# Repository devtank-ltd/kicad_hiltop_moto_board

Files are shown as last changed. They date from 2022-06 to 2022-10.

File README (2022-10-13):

Copyright Devtank Ltd 2021.

This documentation describes Open Hardware and is Licensed under CERN-OHL-W v2.

You may redistribute and modify this documentation under the terms of the CERN-OHL-W v2 (https://cern.ch/cern-ohl). This documentation is distributed WITHOUT ANY EXPRESS OR IMPLIED WARRANTY, INCLUDING OF MERCHANTABILITY, SATISFACTORY QUALITY AND FITNESS FOR A PARTICULAR PURPOSE. Please see the CERN-OHL-W v2 for applicable conditions

Source location: git@github.com:devtank-ltd/kicad_hiltop_loti_board.git 

As per CERN-OHL-W v2 section 4.1, should You produce hardware based on these sources, You must maintain the Source Location visible on the external case of the HILTOP or other product you make using this documentation.

This folder contains HILTOP Moto Board hardware schematics and pcb layout files 

You will need Kicad to open hardware design files.

Moto Boards and other test and measurement products can be purchased directly from Devtank Ltd.

Please contact:
Tim Telford
CTO - Devtank Ltd
+44 (0)1332 650944

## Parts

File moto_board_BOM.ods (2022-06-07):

Title | Moto Board
Revision | Draft
Date | 2019-10-01
Generated | Mon 18 Nov 2019 14:30:10 GMT
Company | Devtank LTD
Comment 1
Comment 2
Comment 3
Comment 4
Total Parts | 204
Total Unique Parts | 68
Ref | Qty | Value | Footprint | Devtank | Dielectric | ESR | Tolerance | Voltage | Voltage | Description | Manufacturer | Manufacturer Part Number | Supplier | Supplier Part number | Cost (unit) | Cost (total)
C1 | 1 | 1uF | Capacitor_SMD:C_0603_1608Metric | 105-014 | X7R |  |  | 16V |  | 1uF 16V X7R | Walsin | 0603B105K160CT | Farnell | 2496835 | 0.128 | 0.128
C2 | 1 | 0.1uF | Capacitor_SMD:C_0402_1005Metric | 105-019 | X7R |  |  | 16V |  | 100nF 50V X7R | Murata Electronics | GRM155R71H104ME14D | Digikey | 490-10701-1-ND | 0.032 | 0.032
C3 | 1 | 0.1uF | Capacitor_SMD:C_0402_1005Metric | 105-019 | X7R | LOW |  |  | 50V | 100nF 50V X7R | Murata Electronics | GRM155R71H104ME14D | Digikey | 490-10701-1-ND | 0.032 | 0.032
C4 | 1 | 0.01uF | Capacitor_SMD:C_0402_1005Metric | 105-029 |  | LOW |  | 50V |  | 0.01uF 50V X7R 0402 | Kemet | C0402C103K5RAC7411 | Mouser | 80-C0402C103K5R7411 | 0.017 | 0.017
C5 | 1 | 1uF | Capacitor_SMD:C_0603_1608Metric | 105-014 | X7R | LOW |  | 16V |  | 1uF 16V X7R | Walsin | 0603B105K160CT | Farnell | 2496835 | 0.128 | 0.128
C6 C7 | 2 | 0.1uF | Capacitor_SMD:C_0402_1005Metric | 105-019 |  |  |  | 50V |  | 100nF 50V X7R | Murata Electronics | GRM155R71H104ME14D | Digikey | 490-10701-1-ND | 0.032 | 0.064
C8 C9 C14 C15 C16 C17 C18 C19 | 8 | 100uF | Capacitor_SMD:CP_Elec_6.3x7.7 | 108-006 |  |  |  | 50V |  | 100uF 50V 0.34R MZR Series | United Chemi-Con | EMZR500ARA101MF80G | Mouser | 661-EMZR500ARA101MF8 | 0.429 | 3.432
C10 C11 | 2 | 10uF | Capacitor_SMD:C_0805_2012Metric | 105-001 |  |  |  |  |  | 10uF 16V X5R 10% MLCC | AVX | 0805YD106KAT2A | Farnell | 1658880 | 0.545 | 1.09
C12 C24 C56 C73 C74 C79 C80 | 7 | 100nF | Capacitor_SMD:C_0402_1005Metric | 105-019 |  |  |  |  |  | 100nF 50V X7R | Murata Electronics | GRM155R71H104ME14D | Digikey | 490-10701-1-ND | 0.032 | 0.224
C13 | 1 | 100uF | Capacitor_SMD:CP_Elec_6.3x7.7 | 108-006 |  |  |  |  |  | 100uF 50V 0.34R MZR Series | United Chemi-Con | EMZR500ARA101MF80G | Mouser | 661-EMZR500ARA101MF8 | 0.429 | 0.429
C52 | 1 | DNF | Capacitor_SMD:C_0603_1608Metric
C55 C102 C104 | 3 | 4.7uF | Capacitor_SMD:C_0402_1005Metric | 105-025 | X5R |  |  | 6.3V |  | 4.7uF 6.3V X5R | muRata | GRM155R60J475ME47D | Farnell | 2426952RL | 0.0565 | 0.1695
C75 C76 | 2 | 18pF | Capacitor_SMD:C_0603_1608Metric | 106-003 |  |  |  |  |  | 18pF COG/NPO | AVX | 06035A180JAT2A | Farnell | 1612182 | 0.0681 | 0.1362
C77 C78 | 2 | 4.3pF | Capacitor_SMD:C_0603_1608Metric | 106-014 |  |  |  |  |  | 4.3pF COG/NPO | Kemet | C0603C439D1HACTU | Mouser | 80-C0603C439D1HACTU | 0.019 | 0.038
C81 C82 | 2 | 100nF | Capacitor_SMD:C_0603_1608Metric | 105-002 |  |  |  |  |  | 100nF 50V X7R | Kemet | C0603C104M5RACTU | Farnell | 2581046 | 0.0413 | 0.0826
C88 C89 | 2 | 33pF | Capacitor_SMD:C_0603_1608Metric | 106-015 |  |  |  |  |  | 33pF COG/NPO | Multicomp Pro | MC0603N330J500CT | Farnell | 1759059 | 0.0311 | 0.0622
C90 | 1 | 0.1uF | Capacitor_SMD:C_0603_1608Metric | 105-002 |  |  |  |  |  | 100nF 50V X7R | Kemet | C0603C104M5RACTU | Farnell | 2581046 | 0.0413 | 0.0413
C91 | 1 | 1.0uF | Capacitor_SMD:C_0402_1005Metric | 105-026 | X5R |  |  | 16V |  | 1uf 16V X5R | Taiyo Yuden | EMK105BJ105KV-F | Farnell | 2113064 | 0.0415 | 0.0415
C92 C94 C95 C96 C97 C98 C99 C101 | 8 | 0.1uF | Capacitor_SMD:C_0402_1005Metric | 105-019 |  |  |  |  |  | 100nF 50V X7R | Murata Electronics | GRM155R71H104ME14D | Digikey | 490-10701-1-ND | 0.032 | 0.256
C100 C103 C105 | 3 | 4.7uF | Capacitor_SMD:C_0402_1005Metric | 105-025 | X5R |  |  | 6.3V |  | 4.7uF 6.3V X5R | muRata | GRM155R60J475ME47D | Farnell | 2426952RL | 0.0565 | 0.1695
C106 | 1 | DNF | Capacitor_SMD:C_0402_1005Metric
D1 | 1 | B240A-13 | Diode_SMD:D_SMA | 133-008 |  |  |  |  |  | B240A-13-F - Schottky Rectifier, 40 V, 2 A, Single, DO-214AC, 2 Pins, 500 mV | Diodes Inc. | B240A-13-F | Farnell | 1843669 | 0.308 | 0.308
D2 | 1 | RED | LED_SMD:LED_0603_1608Metric | 110-001 |  |  |  |  |  | Red LED | ROHM | SML-D12V8WT86C | Farnell | 2687488 | 0.218 | 0.218
D3 D4 D5 | 3 | GRN | LED_SMD:LED_0603_1608Metric | 110-002 |  |  |  |  |  | Green LED | Rohm Semiconductor | SML-D12P8WT86C | Farnell | 2687486 | 0.206 | 0.618
D13 | 1 | GRN | LED_SMD:LED_0603_1608Metric | 110-002 |  |  |  |  |  | Green LED | Rohm Semiconductor | SML-D12P8WT86C | Farnell | 2687486 | 0.214 | 0.214
D32 | 1 | MBR230LSFT1G | Diode_SMD:D_SOD-123 | 133-006 |  |  |  |  |  | Schottky Rectifier, 30 V, 2 A, Single, SOD-123FL | ON Semi | MBR230LSFT1G | Farnell | 2317422 | 0.226 | 0.226
F1 F2 | 2 | Polyfuse | Fuse:Fuse_Bourns_MF-RHT200 | 190-001 |  |  |  |  |  | PPTC Resettable Fuse, Through Hole, MF-RHT Series, 2 A, 3.8 A, 32 V, -40 °C | Bourns Inc | MF-RHT200/32-2 | Mouser | 652-MF-RHT200/32-2 | 0.642 | 1.284
J1 | 1 | Conn_01x04 | Devtank_PCB_Lib:Molex_8981 | 741-001 |  |  |  |  |  | 641737-1 - Wire-To-Board Connector, 5.08 mm, 4 Contacts, Plug, Through Hole, 1 Rows | AMP - TE CONNECTIVITY | 641737-1 | RS Online | 520-254 | 0.99 | 0.99
J2 J4 | 2 | Conn_01x04 | Devtank_PCB_Lib:Phoenix_Contact_SPTAF_4_way_terminal_block | 742-001 |  |  |  |  |  | SPTAF 1/ 4-3,5-EL - Wire-To-Board Terminal Block, 3.5 mm, 4 Ways, 24 AWG, 16 AWG, 1.5 mm², Push In | Phoenix Contact | SPTAF 1/ 4-3,5-EL | Farnell | 2726975 | 1.14 | 2.28
J3 | 1 | Conn_03x32_DIN41612 | Devtank_PCB_Lib:Socket_DIN41612-CaseC1-full-Male-96Pin-3rows_correct | 717-002 |  |  |  |  |  | 406AF-96-MSR-AAE4 (Cards) | Valcon | 406AF-96-MSR-AAE4 | Toby | 406AF-96-MSR-AAE4 | 1.54 | 1.54
J5 | 1 | Conn_02x05_Top_Bottom | Connector_PinHeader_2.54mm:PinHeader_2x05_P2.54mm_Vertical | 710-020 |  |  |  |  |  | 2x5 THD - Valcon 2.54mm Pitch Dual Row Pin Header | Valcon | THD-05-R | Toby | THD-05-R | 0.09 | 0.09
J6 J7 J8 J9 | 4 | Conn_01x04 | Devtank_PCB_Lib:moto_board_4_pin_header |  |  |  |  |  |  | See Below | See Below | See Below | See Below | See Below | See Below
JP1 | 1 | Jumper_NC_Dual | Connector_PinHeader_2.54mm:PinHeader_1x03_P2.54mm_Vertical | 710-014 |  |  |  |  |  | 3 Way Header (shroudless) THS - Valcon 2.54mm Single Row Pin Header | Valcon | THS-03-R | Toby | THS-03-R | 0.04 | 0.04
L1 | 1 | 500mA/0.10DCR | Inductor_SMD:L_0805_2012Metric | 113-004 |  |  |  |  |  | BMB2A0030AN8 30ohm 500ma 0.1ohm 25% | TE Connectivity | BMB2A0030AN8 | Farnell | 2483667 | 0.0874 | 0.0874
L11 | 1 | 2A/0.05DCR | Inductor_SMD:L_0805_2012Metric | 113-002 |  |  |  |  |  | Ferrite 220 ohm, 2 A, WE-CBF Series, 0.05 ohm, ± 25% | Wurth Elektronik | 742792022 | Farnell | 1635733 | 0.172 | 0.172
Q1 Q2 Q3 Q4 Q5 Q6 Q7 Q8 | 8 | CSD18540Q5B | Devtank_PCB_Lib:TI_CSD18540Q5B | 173-004 |  |  |  |  |  | CSD18540Q5B | Texas Instruments | CSD18540Q5B | Mouser | 595-CSD18540Q5B | 1.69 | 13.52
R1 | 1 | DNF | Resistor_SMD:R_1210_3225Metric
R2 R17 R37 R38 R45 R46 R48 R74 R77 R96 R108 R110 | 12 | DNF | Resistor_SMD:R_0603_1608Metric
R3 R8 R9 R10 R11 R12 R21 R24 R25 R26 R27 R28 R33 R34 R35 R36 | 16 | 0R | Resistor_SMD:R_0603_1608Metric | 101-005 |  |  |  |  |  | 0R 0603 75V | Vishay | CRCW06030000Z0EA | Farnell | 1469739 | 0.0149 | 0.2384
R13 | 1 | 0R | Resistor_SMD:R_1210_3225Metric | 101-008 |  |  |  |  |  | 0R 1210 | Vishay | CRCW12100000Z0EA | Farnell | 2309109 | 0.0745 | 0.0745
R14 R99 R102 R105 R111 R120 | 6 | 10K | Resistor_SMD:R_0603_1608Metric | 101-010 |  |  |  |  |  | 10K 1% 75V | Vishay | CRCW060310K0FKEA | Farnell | 1469748 | 0.0148 | 0.0888
R15 R16 | 2 | 4K7 | Resistor_SMD:R_0603_1608Metric | 101-009 |  |  |  |  |  | 4K7 1% 75V | Vishay | CRCW06034K70FKEA | Farnell | 1469807 | 0.0146 | 0.0292
R18 R19 R23 R47 | 4 | 10K | Resistor_SMD:R_0603_1608Metric | 101-010 |  |  |  |  |  | 10K 1% 75V | Vishay | CRCW060310K0FKEA | Farnell | 1469748 | 0.0148 | 0.0592
R20 | 1 | 47K | Resistor_SMD:R_0603_1608Metric | 101-016 |  |  |  |  |  | 47K 1% 50V | Bourns Inc | CR0603-FX-4702ELF | Farnell | 2333548 | 0.0189 | 0.0189
R22 | 1 | 200R | Resistor_SMD:R_0603_1608Metric | 101-059 |  |  |  |  |  | 200R 1% 50V | Multicomp Pro | MCWR06X2000FTL | Farnell | 2447292 | 0.0037 | 0.0037
R29 R30 R31 R32 | 4 | 0.015R | Resistor_SMD:R_2512_6332Metric | 103-006 |  |  | 0.1% |  |  | 0.015R 1% 2W 2512 | Multicomp Pro | MCLRP12DTWSR015 | Farnell | 2828183 | 0.332 | 1.328
R39 R40 R90 R93 | 4 | 100K | Resistor_SMD:R_0603_1608Metric | 101-015 |  |  |  |  |  | 100K 1% 50V | Multicomp Pro | MCWR06X1003FTL | Farnell | 2447226 | 0.0034 | 0.0136
R41 R42 | 2 | 100K | Resistor_SMD:R_0603_1608Metric | 101-015 |  |  |  |  |  | 100K 1% 50V | Multicomp Pro | MCWR06X1003FTL | Farnell | 2447226 | 0.0034 | 0.0068
R43 R44 | 2 | 330R | Resistor_SMD:R_0603_1608Metric | 101-024 |  |  |  |  |  | 330R 1% | Vishay | CRCW0603330RFKEA | Farnell | 1469803 | 0.0146 | 0.0292
R75 | 1 | 10K | Resistor_SMD:R_0603_1608Metric | 101-010 |  |  |  |  |  | 10K 1% 75V | Vishay | CRCW060310K0FKEA | Farnell | 1469748 | 0.0148 | 0.0148
R76 R79 R80 R83 R84 | 5 | 0R | Resistor_SMD:R_0603_1608Metric | 101-005 |  |  |  |  |  | 0R 0603 75V | Vishay | CRCW06030000Z0EA | Farnell | 1469739 | 0.0149 | 0.0745
R78 | 1 | 24K | Resistor_SMD:R_0603_1608Metric | 101-055 |  |  |  |  |  | 24k 1% | Multicomp Pro | MCWR06X2402FTL | Farnell | 2447308 | 0.0034 | 0.0034
R81 R82 R124 | 3 | 330R | Resistor_SMD:R_0603_1608Metric | 101-024 |  |  |  |  |  | 330R 1% | Vishay | CRCW0603330RFKEA | Farnell | 1469803 | 0.0146 | 0.0438
R87 | 1 | 1M | Resistor_SMD:R_0603_1608Metric | 101-056 |  |  |  |  |  | 1M 1% | Multicomp Pro | MCWR06X1004FTL | Farnell | 2447285 | 0.0035 | 0.0035
R109 | 1 | 12.0K | Resistor_SMD:R_0603_1608Metric | 101-044 |  |  | 1% |  |  | 12K 1% 50V 100mW | Bourns Inc | CR0603-FX-1202ELF | Farnell | 2333583 | 0.0172 | 0.0172
R112 | 1 | DNF | Resistor_SMD:R_0603_1608Metric
SW1 | 1 | SW_Push | Button_Switch_SMD:SW_SPST_B3U-1000P | 780-001 |  |  |  |  |  | Switch SMT Micro SPST-NO | Omron | B3U-1000P | Digikey | SW1020CT-ND | 0.624 | 0.624
TP1 TP2 TP3 TP4 TP5 TP6 TP7 TP8 TP9 TP10 TP11 TP12 TP13 TP14 TP15 TP16 TP17 TP18 TP19 TP20 TP21 TP22 TP23 TP24 TP25 TP26 TP27 TP28 TP29 TP30 TP31 TP32 TP33 TP34 TP35 TP36 TP37 TP38 TP101 TP102 TP103 TP104 TP105 TP126 | 44 | Test_Point | TestPoint:TestPoint_THTPad_D1.0mm_Drill0.5mm
U1 | 1 | DRV8704 | Devtank_PCB_Lib:DRV8704 | 123-012 |  |  |  |  |  | DRV8704DCPR dual h-bridge and pwm chip | Texas Instruments | DRV8704DCPR | Digikey | 296-43248-1-ND | 3.17 | 3.17
U2 | 1 | LD1117S33TR_SOT223 | Package_TO_SOT_SMD:SOT-223-3_TabPin2 | 150-004 |  |  |  |  |  | LM1117IMP-3.3 Fixed LDO Regulator 3.3V | Texas Instruments | LM1117IMP-3.3/NOPB | Digikey | LM1117IMP-3.3/NOPBCT-ND | 0.762 | 0.762
U3 | 1 | AT25DN512CSSHF-B | Package_SO:SOIC-8_3.9x4.9mm_P1.27mm | 129-002 |  |  |  |  |  | 512K, 2.3V, 104MHz Serial Flash | Adesto | AT25DN512C-SSHF-B (https://www.mouser.co.uk/ProductDetail/Adesto-Technologies/AT25DN512C-SSHF-B) | Mouser | 988-AT25DN512CSSHF-B | 0.233 | 0.233
U7 | 1 | DNF | Package_SO:SOIC-8_3.9x4.9mm_P1.27mm
U13 | 1 | CP2102N-A01-GQFN24 | Package_DFN_QFN:QFN-24-1EP_4x4mm_P0.5mm_EP2.6x2.6mm_ThermalVias | 118-007 |  |  |  |  |  | CP2102N USB to UART adapter IC | Silicon Labs | CP2102N-A01-GQFN24 | Digikey | 336-3693-ND | 1.04 | 1.04
U22 | 1 | STM32F072RBTx | Package_QFP:LQFP-64_10x10mm_P0.5mm | 126-001 |  |  |  |  |  | STM32F072RBT6, 32bit ARM Cortex M0 Microcontroller, 48MHz, 64 kB, 128 kB Flash | ST Microelectronics | STM32F072RBT6 | Digikey | 497-14644-ND | 2.733 | 2.733
U27 | 1 | USB2502 | Package_DFN_QFN:QFN-36-1EP_6x6mm_P0.5mm_EP3.7x3.7mm | 118-012 |  |  |  |  |  | USB2502 | Microchip | USB2502-AEZG | Mouser | 886-USB2502-AEZG | £1.93 | £1.93
Y1 | 1 | 50ppm 24.000MHZ | Crystal:Crystal_SMD_TXC_7A-2Pin_5x3.2mm | 181-011 |  |  |  |  |  | TXC 24MHz crystal 30ppm | TXC | 7A-24.000MAHE-T | Mouser | 717-7A-24.000MAHE-T | 0.496 | 0.496
Y2 | 1 | 8MHZ | Crystal:Crystal_SMD_Abracon_ABM3C-4Pin_5.0x3.2mm | 181-009 |  |  |  |  |  | ABM3B-8.000MHZ-B2-T - Crystal, 8 MHz, SMD, 5mm x 3.2mm, 50 ppm, 18 pF, 20 ppm | Abracon | ABM3B-8.000MHZ-B2-T | RS | 171-0644 | 0.323 | 0.323
Y3 | 1 | ABS25-32.768KHZ-6-T | Crystal:Crystal_SMD_7050-4Pin_7.0x5.0mm | 181-008 |  |  |  |  |  | Crystal, 32.768 kHz, SMD, 8mm x 3.8mm | Abracon | ABS25-32.768KHZ-6-T | RS | 171-2795 | 0.323 | 0.323
 |  |  |  |  |  |  |  |  |  |  |  |  |  |  |  | 41.8417
For J6 J7 J8 J9 two parts required
J6 J7 J8 J9 | 4 |  |  | 710-014 |  |  |  |  |  | 3 Way Header (shroudless) | Valcon | THS-03-R | Toby | THS-03-R | 0.04 | 0.16
J6 J7 J8 J9 | 4 |  |  | 710-022 |  |  |  |  |  | 1 Way Header (shroudless) | Valcon | THS-01-R (https://www.toby.co.uk/board-to-board-pcb-connectors/254mm-headers/ths-valcon-254mm-single-row-pin-header/THS-01-R/) | Toby | THS-01-R (https://www.toby.co.uk/board-to-board-pcb-connectors/254mm-headers/ths-valcon-254mm-single-row-pin-header/THS-01-R/) | 0.02 | 0.08
 |  |  |  |  |  |  |  |  |  |  |  |  |  |  | Total | 0.24
BOM made with KICAD_BOM_WIZARD (https://github.com/HashDefineElectronics/KiCad_BOM_Wizard.git)
Generated Mon 18 Nov 2019 14:30:10 GMT |  |  |  |  |  |  |  |  |  |  |  |  |  | Complete total | 42.0817

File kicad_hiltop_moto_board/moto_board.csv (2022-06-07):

Title | Sensi Board
Revision | Draft
Date | 2019-10-01
Generated | Mon 18 Nov 2019 14:30:10 GMT
Company
Comment 1
Comment 2
Comment 3
Comment 4
Total Parts | 204
Total Unique Parts | 68
Ref | Qty | Value | Footprint | Datasheet | Devtank | Dielectric | ESR | Tolerance | Voltage | Voltage
C1 | 1 | 1uF | Capacitor_SMD:C_0603_1608Metric |  |  | X7R |  |  | 6.3V
C2 | 1 | 0.1uF | Capacitor_SMD:C_0402_1005Metric |  |  | X7R |  |  | 10V
C3 | 1 | 0.1uF | Capacitor_SMD:C_0402_1005Metric |  |  | X7R | LOW |  |  | 50V
C4 | 1 | 0.01uF | Capacitor_SMD:C_0402_1005Metric |  |  |  | LOW |  | 50V
C5 | 1 | 1uF | Capacitor_SMD:C_0603_1608Metric |  |  | X7R | LOW |  | 16V
C6 C7 | 2 | 0.1uF | Capacitor_SMD:C_0402_1005Metric |  |  |  |  |  | 50V
C8 C9 C14 C15 C16 C17 C18 C19 | 8 | 100uF | Capacitor_SMD:CP_Elec_6.3x7.7 |  |  |  |  |  | 50V
C10 C11 | 2 | 10uF | Capacitor_SMD:C_0805_2012Metric |  | 105-001
C12 C24 C56 C73 C74 C79 C80 | 7 | 100nF | Capacitor_SMD:C_0402_1005Metric |  | 105-019
C13 | 1 | 100uF | Capacitor_SMD:CP_Elec_6.3x7.7 |  | 108-003
C52 | 1 | DNF | Capacitor_SMD:C_0603_1608Metric
C55 C102 C104 | 3 | 4.7uF | Capacitor_SMD:C_0402_1005Metric |  | 105-025 | X5R |  |  | 6.3V
C75 C76 | 2 | 18pF | Capacitor_SMD:C_0603_1608Metric |  | 106-003
C77 C78 | 2 | 4.3pF | Capacitor_SMD:C_0603_1608Metric |  | 106-014
C81 C82 | 2 | 100nF | Capacitor_SMD:C_0603_1608Metric |  | 105-002
C88 C89 | 2 | 33pF | Capacitor_SMD:C_0603_1608Metric |  | 106-015
C90 | 1 | 0.1uF | Capacitor_SMD:C_0603_1608Metric |  | 105-002
C91 | 1 | 1.0uF | Capacitor_SMD:C_0402_1005Metric |  | 105-026 | X5R |  |  | 16V
C92 C94 C95 C96 C97 C98 C99 C101 | 8 | 0.1uF | Capacitor_SMD:C_0402_1005Metric |  | 105-019
C100 C103 C105 | 3 | 4.7uF | Capacitor_SMD:C_0402_1005Metric |  | 105-025 | X5R |  |  | 6.3V
C106 | 1 | DNF | Capacitor_SMD:C_0402_1005Metric |  | 105-019
D1 | 1 | B240A-13 | Diode_SMD:D_SMA |  | 133-008
D2 | 1 | RED | LED_SMD:LED_0603_1608Metric | ~
D3 D4 D5 | 3 | GRN | LED_SMD:LED_0603_1608Metric | ~
D13 | 1 | GRN | LED_SMD:LED_0603_1608Metric | ~ | 110-002
D32 | 1 | MBR230LSFT1G | Diode_SMD:D_SOD-123 |  | 133-006
F1 F2 | 2 | Polyfuse | Fuse:Fuse_Bourns_MF-RHT200
J1 | 1 | Conn_01x04 | Devtank_PCB_Lib:Molex_8981 | ~
J2 J4 | 2 | Conn_01x04 | Devtank_PCB_Lib:Phoenix_Contact_SPTAF_4_way_terminal_block | ~
J3 | 1 | Conn_03x32_DIN41612 | Devtank_PCB_Lib:Socket_DIN41612-CaseC1-full-Male-96Pin-3rows_correct |  | 717-002
J5 | 1 | Conn_02x05_Top_Bottom | Connector_PinHeader_2.54mm:PinHeader_2x05_P2.54mm_Vertical | ~
J6 J7 J8 J9 | 4 | Conn_01x04 | Devtank_PCB_Lib:moto_board_4_pin_header | ~
JP1 | 1 | Jumper_NC_Dual | Connector_PinHeader_2.54mm:PinHeader_1x03_P2.54mm_Vertical |  | 710-014
L1 | 1 | 500mA/0.10DCR | Inductor_SMD:L_0805_2012Metric
L11 | 1 | 2A/0.05DCR | Inductor_SMD:L_0805_2012Metric |  | 113-002
Q1 Q2 Q3 Q4 Q5 Q6 Q7 Q8 | 8 | CSD18540Q5B | Devtank_PCB_Lib:TI_CSD18540Q5B | http://www.ti.com/lit/gpn/csd18540q5b
R1 | 1 | DNF | Resistor_SMD:R_1210_3225Metric
R2 R17 R37 R38 R45 R46 R48 R74 R77 R96 R108 R110 | 12 | DNF | Resistor_SMD:R_0603_1608Metric
R3 R8 R9 R10 R11 R12 R21 R24 R25 R26 R27 R28 R33 R34 R35 R36 | 16 | 0R | Resistor_SMD:R_0603_1608Metric
R13 | 1 | 0R | Resistor_SMD:R_1210_3225Metric
R14 R99 R102 R105 R111 R120 | 6 | 10K | Resistor_SMD:R_0603_1608Metric |  | 101-010
R15 R16 | 2 | 4K7 | Resistor_SMD:R_0603_1608Metric |  | 101-009
R18 R19 R23 R47 | 4 | 10K | Resistor_SMD:R_0603_1608Metric
R20 | 1 | 47K | Resistor_SMD:R_0603_1608Metric |  | 101-016
R22 | 1 | 200R | Resistor_SMD:R_0603_1608Metric
R29 R30 R31 R32 | 4 | 0.015R | Resistor_SMD:R_2512_6332Metric |  |  |  |  | 0.1%
R39 R40 R90 R93 | 4 | 100K | Resistor_SMD:R_0603_1608Metric |  | 101-015
R41 R42 | 2 | 100K | Resistor_SMD:R_0603_1608Metric
R43 R44 | 2 | 330R | Resistor_SMD:R_0603_1608Metric
R75 | 1 | 10K | Resistor_SMD:R_0603_1608Metric |  | 101-010
R76 R79 R80 R83 R84 | 5 | 0R | Resistor_SMD:R_0603_1608Metric |  | 101-005
R78 | 1 | 24K | Resistor_SMD:R_0603_1608Metric |  | 101-055
R81 R82 R124 | 3 | 330R | Resistor_SMD:R_0603_1608Metric |  | 101-024
R87 | 1 | 1M | Resistor_SMD:R_0603_1608Metric |  | 101-056
R109 | 1 | 12.0K | Resistor_SMD:R_0603_1608Metric |  | 101-044 |  |  | 1%
R112 | 1 | DNF | Resistor_SMD:R_0603_1608Metric |  | 101-010
SW1 | 1 | SW_Push | Button_Switch_SMD:SW_SPST_B3U-1000P |  | 780-001
TP1 TP2 TP3 TP4 TP5 TP6 TP7 TP8 TP9 TP10 TP11 TP12 TP13 TP14 TP15 TP16 TP17 TP18 TP19 TP20 TP21 TP22 TP23 TP24 TP25 TP26 TP27 TP28 TP29 TP30 TP31 TP32 TP33 TP34 TP35 TP36 TP37 TP38 TP101 TP102 TP103 TP104 TP105 TP126 | 44 | Test_Point | TestPoint:TestPoint_THTPad_D1.0mm_Drill0.5mm | ~
U1 | 1 | DRV8704 | Devtank_PCB_Lib:DRV8704 | http://www.ti.com/lit/ds/slvsc40f/slvsc40f.pdf
U2 | 1 | LD1117S33TR_SOT223 | Package_TO_SOT_SMD:SOT-223-3_TabPin2 | http://www.st.com/st-web-ui/static/active/en/resource/technical/document/datasheet/CD00000544.pdf | 150-004
U3 | 1 | AT25DN512CSSHF-B | Package_SO:SOIC-8_3.9x4.9mm_P1.27mm | http://www.atmel.com/products/Memories/serial/spi.aspx | 129-002
U7 | 1 | DNF | Package_SO:SOIC-8_3.9x4.9mm_P1.27mm |  | 129-006
U13 | 1 | CP2102N-A01-GQFN24 | Package_DFN_QFN:QFN-24-1EP_4x4mm_P0.5mm_EP2.6x2.6mm_ThermalVias | http://www.silabs.com/support%20documents/technicaldocs/cp2102n-datasheet.pdf | 118-007
U22 | 1 | STM32F072RBTx | Package_QFP:LQFP-64_10x10mm_P0.5mm | http://www.st.com/st-web-ui/static/active/en/resource/technical/document/datasheet/DM00090510.pdf | 126-001
U27 | 1 | USB2502 | Package_DFN_QFN:QFN-36-1EP_6x6mm_P0.5mm_EP3.7x3.7mm | DOCUMENTATION | 118-012
Y1 | 1 | 50ppm 24.000MHZ | Crystal:Crystal_SMD_TXC_7A-2Pin_5x3.2mm |  | 181-010
Y2 | 1 | 8MHZ | Crystal:Crystal_SMD_Abracon_ABM3C-4Pin_5.0x3.2mm |  | 181-009
Y3 | 1 | ABS25-32.768KHZ-6-T | Crystal:Crystal_SMD_7050-4Pin_7.0x5.0mm |  | 181-008
BOM made with KICAD_BOM_WIZARD (https://github.com/HashDefineElectronics/KiCad_BOM_Wizard.git)
Generated Mon 18 Nov 2019 14:30:10 GMT

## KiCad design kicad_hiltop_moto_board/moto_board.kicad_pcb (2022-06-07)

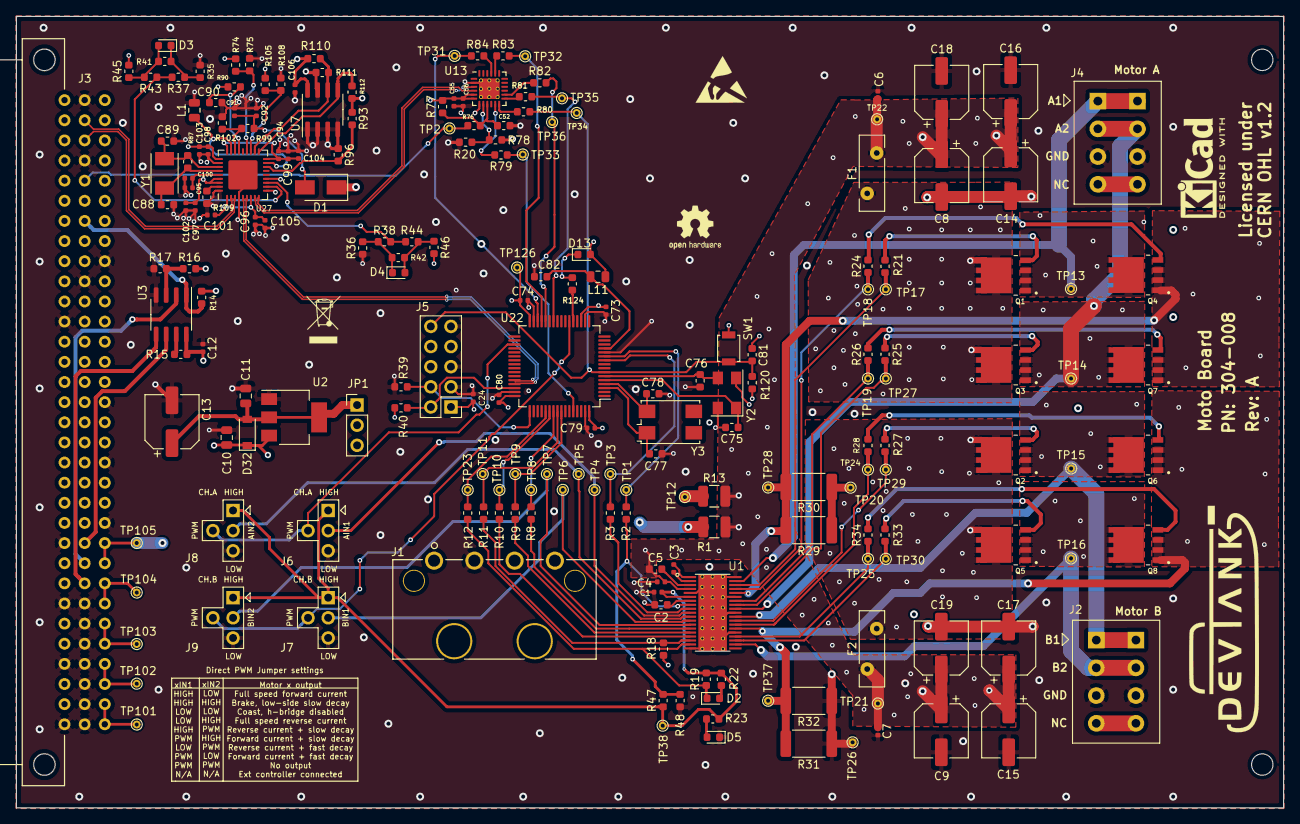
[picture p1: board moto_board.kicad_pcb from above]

Board: 4 copper layers, 159.9 x 99.9 mm, 204 parts (0 on the bottom side), 117 nets.

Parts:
C1, C5: 1uF; C_0603_1608Metric
C2, C3, C6, C7, C92, C94, C95, C96, C97, C98, C99, C101: 0.1uF; C_0402_1005Metric
C4: 0.01uF; C_0402_1005Metric
C8, C9, C13, C14, C15, C16, C17, C18, C19: 100uF; CP_Elec_6.3x7.7
C10, C11: 10uF; C_0805_2012Metric
C12, C24, C56, C73, C74, C79, C80: 100nF; C_0402_1005Metric
C52: DNF; C_0603_1608Metric
C55, C100, C102, C103, C104, C105: 4.7uF; C_0402_1005Metric
C75, C76: 18pF; C_0603_1608Metric
C77, C78: 4.3pF; C_0603_1608Metric
C81, C82: 100nF; C_0603_1608Metric
C88, C89: 33pF; C_0603_1608Metric
C90: 0.1uF; C_0603_1608Metric
C91: 1.0uF; C_0402_1005Metric
C106: DNF; C_0402_1005Metric
D1: B240A-13; D_SMA
D2: RED; LED_0603_1608Metric
D3, D4, D5, D13: GRN; LED_0603_1608Metric
D32: MBR230LSFT1G; D_SOD-123
F1, F2: Polyfuse; Fuse_Bourns_MF-RHT200
J1: Conn_01x04; Molex_8981
J2, J4: Conn_01x04; Phoenix_Contact_SPTAF_4_way_terminal_block
J3: Conn_03x32_DIN41612; Socket_DIN41612-CaseC1-full-Male-96Pin-3rows_correct
J5: Conn_02x05_Top_Bottom; PinHeader_2x05_P2.54mm_Vertical
J6, J7, J8, J9: Conn_01x04; moto_board_4_pin_header
JP1: Jumper_NC_Dual; PinHeader_1x03_P2.54mm_Vertical
L1: 500mA/0.10DCR; L_0805_2012Metric
L11: 2A/0.05DCR; L_0805_2012Metric
Q1, Q2, Q3, Q4, Q5, Q6, Q7, Q8: CSD18540Q5B; TI_CSD18540Q5B
R1: DNF; R_1210_3225Metric
R2, R17, R37, R38, R45, R46, R48, R74, R77, R96, R108, R110, R112: DNF; R_0603_1608Metric
R3, R8, R9, R10, R11, R12, R21, R24, R25, R26, R27, R28, R33, R34, R35, R36, R76, R79, R80, R83, R84: 0R; R_0603_1608Metric
R13: 0R; R_1210_3225Metric
R14, R18, R19, R23, R47, R75, R99, R102, R105, R111, R120: 10K; R_0603_1608Metric
R15, R16: 4K7; R_0603_1608Metric
R20: 47K; R_0603_1608Metric
R22: 200R; R_0603_1608Metric
R29, R30, R31, R32: 0.015R; R_2512_6332Metric
R39, R40, R41, R42, R90, R93: 100K; R_0603_1608Metric
R43, R44, R81, R82, R124: 330R; R_0603_1608Metric
R78: 24K; R_0603_1608Metric
R87: 1M; R_0603_1608Metric
R109: 12.0K; R_0603_1608Metric
SW1: SW_Push; SW_SPST_B3U-1000P
TP1, TP2, TP3, TP4, TP5, TP6, TP7, TP8, TP9, TP10, TP11, TP12, TP13, TP14, TP15, TP16, TP17, TP18, TP19, TP20, TP21, TP22, TP23, TP24, TP25, TP26, TP27, TP28, TP29, TP30, TP31, TP32, TP33, TP34, TP35, TP36, TP37, TP38, TP101, TP102, TP103, TP104, TP105, TP126: Test_Point; TestPoint_THTPad_D1.0mm_Drill0.5mm
U1: DRV8704
U2: LD1117S33TR_SOT223; SOT-223-3_TabPin2
U3: AT25DN512CSSHF-B; SOIC-8_3.9x4.9mm_P1.27mm
U7: DNF; SOIC-8_3.9x4.9mm_P1.27mm
U13: CP2102N-A01-GQFN24; QFN-24-1EP_4x4mm_P0.5mm_EP2.6x2.6mm_ThermalVias
U22: STM32F072RBTx; LQFP-64_10x10mm_P0.5mm
U27: USB2502; QFN-36-1EP_6x6mm_P0.5mm_EP3.7x3.7mm
Y1: 50ppm 24.000MHZ; Crystal_SMD_TXC_7A-2Pin_5x3.2mm
Y2: 8MHZ; Crystal_SMD_Abracon_ABM3C-4Pin_5.0x3.2mm
Y3: ABS25-32.768KHZ-6-T; Crystal_SMD_7050-4Pin_7.0x5.0mm

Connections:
+3V3: C12.2, C24.1, C55.1, C56.1, C73.1, C74.1, C79.1, C80.1, C96.1, C97.1, C98.1, C101.1, C102.1, C103.1, C105.1, C106.1, D13.2, J5.1, JP1.2, L11.1, R14.2, R15.2, R16.2, R18.2, R40.1, R45.2, R46.2, R74.1, R77.2, R90.1, R93.1, R105.2, R110.2, R112.1, R120.1, TP126.1, U3.8, U7.8, U13.5, U13.6, U13.7, U22.19, U22.32, U22.48, U22.64, U27.1, U27.7, U27.13, U27.28, U27.33, U27.34
+3V3_BP: J3.7c, J3.8c, JP1.3, TP104.1
+3V3_LOC: C11.2, C13.1, D32.2, JP1.1, U2.2
+5V: C10.2, D1.1, D32.1, J3.3c, J3.4c, R78.2, TP102.1, U2.3
+12V: J3.1c, J3.2c, TP101.1
-5V: J3.5c, J3.6c, TP103.1
/12V_EXT: J1.1, R13.1, TP12.1
/A1: J4.1, Q1.1, Q4.3, TP13.1, U1.37
/A2: J4.2, Q3.1, Q7.3, TP14.1, U1.30
/B1: J2.1, Q2.1, Q6.3, TP15.1, U1.28
/B2: J2.2, Q5.1, Q8.3, TP16.1, U1.21
/M_AIN1: J6.2, TP4.1, U1.10
/M_AIN2: J8.2, TP5.1, U1.11
/M_BIN1: J7.2, TP6.1, U1.12
/M_BIN2: J9.2, TP7.1, U1.13
/M_FAULTn: R12.2, TP23.1, U22.53
/M_RESET: R3.2, TP3.1, U22.10
/M_SCLK: R8.2, TP8.1, U22.55
/M_SCS: R10.2, TP10.1, U22.54
/M_SDATI: R9.2, TP9.1, U22.57
/M_SDATO: R11.2, TP11.1, U22.56
/M_SLEEPn: R2.2, TP1.1, U22.11
/PORT_SEL: J3.26b, R14.1, U3.1
/PWM_1: J6.4, J8.4, U22.35
/PWM_2: J7.4, J9.4, U22.22
/RESET: J3.28b, R76.2, TP2.1
/SPI0_CLK: J3.10b, U3.6
/SPI0_MISO: J3.9b, U3.2
/SPI0_MOSI: J3.8b, U3.5
/STM_BOOT0: R79.1, TP33.1, U22.60
/STM_DEBUG_RX: R84.1, TP31.1, U22.30
/STM_DEBUG_TX: R83.1, TP32.1, U22.29
/STM_RES1: R81.1, TP35.1, U22.26
/STM_RES2: R82.1, TP36.1, U22.28
/STM_RESET: C81.1, J5.10, R80.1, R120.2, SW1.2, TP34.1, U22.7
/STM_USB_DATA_N: U22.44, U27.5
/STM_USB_DATA_P: U22.45, U27.6
/SWD_IO: J5.2, R40.2, U22.46
/SWD_SCK: J5.4, R39.1, U22.49
/USB_DATA_N: J3.30b, U27.3
/USB_DATA_P: J3.31b, U27.2
/USB_DEBUG_N: U13.4, U27.9
/USB_DEBUG_P: U13.3, U27.8
/V5: C2.1, J6.1, J7.1, J8.1, J9.1, R19.2, R22.1, R23.1, R47.1, TP38.1, U1.6
/VM: C4.2, C5.1, C6.1, C7.1, C8.1, C9.1, C14.1, C15.1, C16.1, C17.1, C18.1, C19.1, F1.2, F2.1, R1.2, R13.2, TP21.1, TP22.1, U1.4
/motor_control/FAULTn: D2.1, R12.1, R19.1, U1.18
/motor_control/RESET: R3.1, U1.9
/motor_control/SCLK: R8.1, U1.14
/motor_control/SCS: R10.1, U1.16
/motor_control/SDATI: R9.1, U1.15
/motor_control/SDATO: R11.1, R18.1, U1.17
/motor_control/SLEEPn: R2.1, R47.2, R48.2, U1.8
ADJ_DC: J3.9c, J3.10c, R1.1, TP105.1
GND: C1.1, C2.2, C4.1, C6.2, C7.2, C8.2, C9.2, C10.1, C11.1, C12.1, C13.2, C14.2, C15.2, C16.2, C17.2, C18.2, C19.2, C24.2, C52.2, C55.2, C56.2, C73.2, C74.2, C75.2, C76.2, C77.2, C78.2, C79.2, C80.2, C81.2, C82.2, C88.2, C89.1, C90.2, C91.2, C92.2, C94.2, C95.2, C96.2, C97.2, C98.2, C99.2, C100.2, C101.2, C102.2, C103.2, C104.2, C105.2, C106.2, D5.1, J1.2, J1.3, J2.3, J3.1a, J3.1b, J3.2b, J3.3b, J3.4a, J3.4b, J3.5b, J3.6b, J3.7a, J3.7b, J3.10a, J3.11c, J3.13b, J3.14c, J3.17c, J3.21a, J3.23b, J3.24c, J3.29b, J3.32b, J4.3, J5.3, J5.5, J5.9, J6.3, J7.3, J8.3, J9.3, L1.1, R17.1, R20.1, R29.1, R30.1, R31.1, R32.1, R35.1, R36.1, R39.2, R48.1, R75.1, R96.1, R102.2, R108.2, R109.2, R111.2, SW1.1, TP20.1, TP26.1, U1.5, U1.19, U1.24, U1.29, U1.33, U1.38, U1.39, U2.1, U3.4, U7.1, U7.2, U7.3, U7.4, U7.7, U13.2, U13.25, U22.12, U22.18, U22.31, U22.47, U22.63, U27.4, U27.10, U27.29, U27.36, U27.37, Y2.2, Y2.4
unnamed: C1.2, U1.7
unnamed: C3.1, U1.1
unnamed: C3.2, U1.2
unnamed: C5.2, U1.3
unnamed: C52.1, R76.1, R77.1, U13.9
unnamed: C75.1, U22.5, Y2.1
unnamed: C76.1, U22.6, Y2.3
unnamed: C77.1, U22.3, Y3.1
unnamed: C78.1, U22.4, Y3.4
unnamed: C82.1, L11.2, U22.13
unnamed: C88.1, R87.1, U27.31, Y1.2
unnamed: C89.2, R87.2, U27.30, Y1.1
unnamed: C90.1, R90.2, U27.24
unnamed: C91.1, C92.1, D1.2, R99.1
unnamed: C95.1, C100.1, U27.32
unnamed: C94.1, C99.1, C104.1, U27.18, U27.27
unnamed: D2.2, R22.2
unnamed: D3.1, R35.2, R37.1, R41.1
unnamed: D3.2, R41.2, R43.2, R45.1
unnamed: D4.1, R36.2, R38.1, R42.1
unnamed: D4.2, R42.2, R44.2, R46.1
unnamed: D5.2, R23.2
unnamed: D13.1, R124.1
unnamed: F1.1, Q1.3, Q3.3
unnamed: F2.2, Q2.3, Q5.3
unnamed: L1.2, U27.17, U27.26
unnamed: Q1.2, R21.2
unnamed: Q2.2, R27.2
unnamed: Q3.2, R25.2
unnamed: Q4.1, Q7.1, R29.2, R30.2, TP28.1, U1.34
unnamed: Q4.2, R24.2
unnamed: Q5.2, R33.2
unnamed: Q6.1, Q8.1, R31.2, R32.2, TP37.1, U1.25
unnamed: Q6.2, R28.2
unnamed: Q7.2, R26.2
unnamed: Q8.2, R34.2
unnamed: R15.1, U3.7
unnamed: R16.1, R17.2, U3.3
unnamed: R20.2, R78.1, U13.8
unnamed: R21.1, TP17.1, U1.36
unnamed: R24.1, TP18.1, U1.35
unnamed: R25.1, TP27.1, U1.31
unnamed: R26.1, TP19.1, U1.32
unnamed: R27.1, TP29.1, U1.27
unnamed: R28.1, TP24.1, U1.26
unnamed: R33.1, TP30.1, U1.22
unnamed: R34.1, TP25.1, U1.23
unnamed: R37.2, R43.1, U27.11
unnamed: R38.2, R44.1, U27.12
unnamed: R74.2, R75.2, U27.22
unnamed: R79.2, U13.11
unnamed: R80.2, U13.12
unnamed: R81.2, U13.13
unnamed: R82.2, U13.14
unnamed: R83.2, U13.20
unnamed: R84.2, U13.21
unnamed: R93.2, R96.2, U27.16
unnamed: R99.2, R102.1, U27.25
unnamed: R105.1, R108.1, U27.21
unnamed: R109.1, U27.35
unnamed: R110.1, R111.1, U7.6, U27.20
unnamed: R112.2, U7.5, U27.19
unnamed: R124.2, U22.21

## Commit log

2019-10-31 Setup common libraries for my Kicad project.
2019-10-31 merged fils into new repo
    [Motor control.sch, Motor_Control_Board.csv, Motor_Control_Board.kicad_pcb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]
2019-10-31 Unused pind removed from moto board
    [Motor_Control_Board.csv, Motor_Control_Board.xml, Motor_Control_Board_BOM.xml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]
2019-11-04 Started on moto board layout
    [STM_Micro.sch, USB_Debug.sch, moto_board.kicad_pcb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]
2019-11-04 Rough layout of moto board
    [USB2502 Hub Controller.sch, moto_board.kicad_pcb, moto_board.sch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]
2019-11-08 Updated moto board schematic and layout
    [moto_board.kicad_pcb, moto_board.sch, motor_control.sch]
2019-11-08 Moto vboard test points added
    [motor_control.sch]
2019-11-13 Moto board awaiting review
    [STM_Micro.sch, USB2502 Hub Controller.sch, c-0641737-01-g-3d.stp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]
2019-11-15 Moto board connectors moved
    [STM_Micro.sch, moto_board.kicad_pcb, motor_control.sch]
2019-11-15 moto board 3d connector models added
    [moto_board.kicad_pcb]
2019-11-18 Updated moto board
    [moto_board.kicad_pcb]
2019-11-18 Moto board csd mosfet footprint changes
    [CSD18540Q5B.stp, DRV8704.stp, moto_board.kicad_pcb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]
2019-11-18 Moto Board Rev A
    [moto_board.kicad_pcb]
2022-06-07 added bom
    [CSD18540Q5B.stp, DRV8704.stp, USB2502 Hub Controller.sch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]

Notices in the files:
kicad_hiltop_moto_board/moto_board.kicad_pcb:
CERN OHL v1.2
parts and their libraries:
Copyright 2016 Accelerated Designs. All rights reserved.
